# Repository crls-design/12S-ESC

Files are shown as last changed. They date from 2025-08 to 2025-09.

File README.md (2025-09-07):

# 12S ESC

This repository provides a low-cost, open-source design for a 12S Electronic Speed Controller (ESC) geared towards heavy-lift multirotor applications. It is designed to work with [ESCape32](https://github.com/neoxic/ESCape32), an open-source 32-bit ESC firmware.

## Design Philosophy

The goal of this ESC design is to maximize the performance-to-cost ratio by utilizing readily available components and open-source firmware while maintaining electrical and thermal characteristics that meet or exceed those of commercial ESCs in the same class.

This project aims to offer a competitive alternative to proprietary ESCs used in drones, robotics, and other high-power applications.

## Specifications

- STM32G431 processor
- 24MHz HSE crystal resonator
- 12S input (up to 50.4V)
- Full support for [ESCape32](https://github.com/neoxic/ESCape32)

> [!NOTE]  
> Although these are designed for 12S, the actual hardware is rated for 100V which is nearly double.

## Gallery

<p align="center">
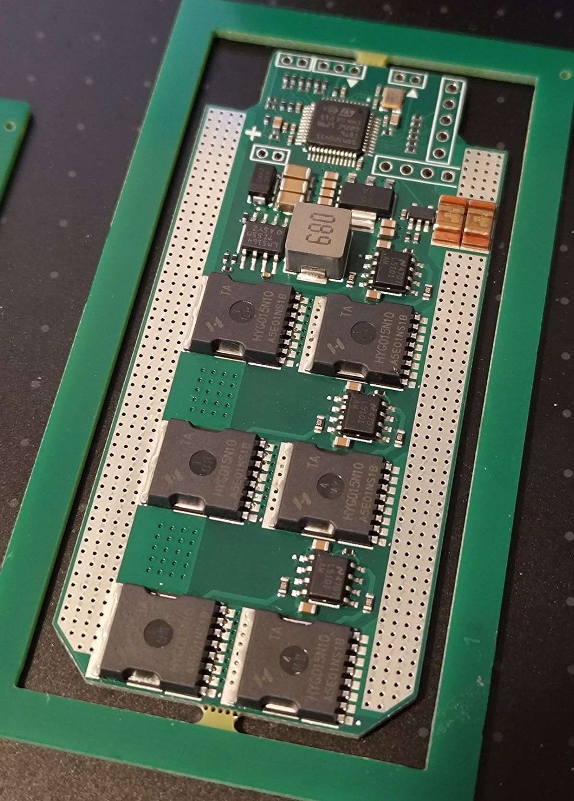
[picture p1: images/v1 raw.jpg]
    
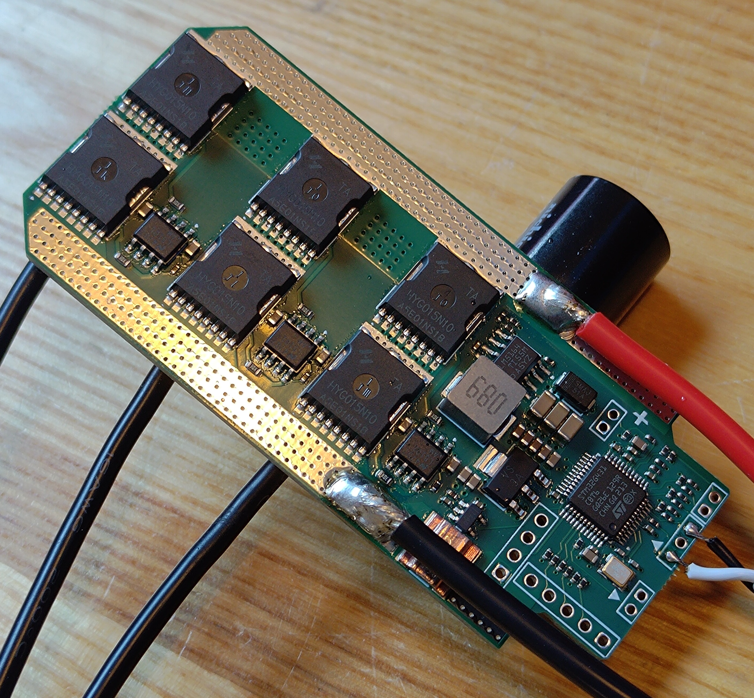
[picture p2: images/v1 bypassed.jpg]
    
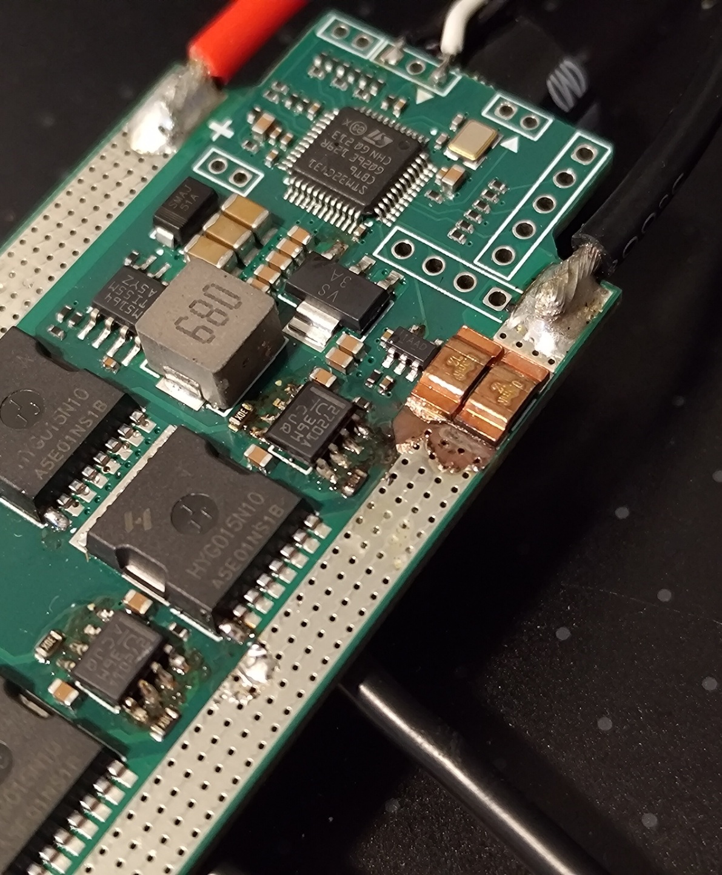
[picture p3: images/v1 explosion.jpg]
    
    </br>
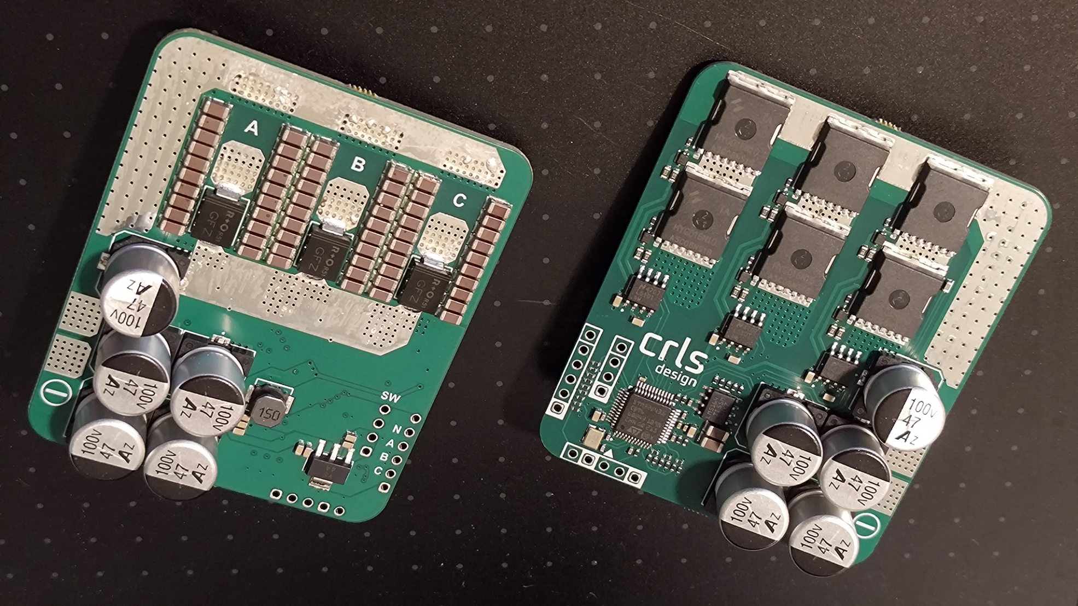
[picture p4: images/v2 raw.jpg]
    
</p>

## Getting Started

See [Getting Started](./docs/getting-started.md) for instructions on flashing and setup.

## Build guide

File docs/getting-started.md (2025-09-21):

# Getting Started

## Flashing and Setup

For blank STM32s, these are the general steps to get the board up and running:

1. Configuring the option bytes.
2. Flashing the appropriate bootloader.
3. Flashing the firmware.

> [!WARNING]  
> Do **not** power the board with a battery before completing these steps. The gate drivers do not have shoot-through protection, and powering prematurely will damage the MOSFETs.

### Prerequisites

- ST-LINK
- [STM32CubeProgrammer](https://www.st.com/en/development-tools/stm32cubeprog.html)

### Option Bytes

1. Always run from flash.

    - BOOT_LOCK = 1

2. Disable read/write protection (if not set by default).

    - RDP = AA (Level 0)
    - Flash protection = disabled

### Bootloader

 Get the latest `BOOT4_PA2` bootloader binary from [https://github.com/neoxic/ESCape32/releases](https://github.com/neoxic/ESCape32/releases) and flash at address `0x08000000`.

### Firmware

Build the following baseline target(s) and flash at address `0x08001000`.

**v1:**

```
add_target(CRLS1 STM32G431 DEAD_TIME=240 COMP_MAP=123 HALL_MAP=0xB450 SENS_MAP=0xB2A6A7 VOLT_MUL=3130 CURR_MUL=20 TEMP_ADC2 TEMP_CHAN=12 TEMP_FUNC=NTC10K3455UP2K USE_XOR USE_HSE=24 DUTY_SPUP=10 DUTY_RATE=5 FREQ_MIN=24 FREQ_MAX=24 TELEM_MODE=1 TELEM_POLES=2)
```

**v2:**

```
add_target(CRLS2 STM32G431 DEAD_TIME=160 COMP_MAP=231 HALL_MAP=0xB450 SENS_MAP=0xB2A6A7 VOLT_MUL=3130 TEMP_ADC2 TEMP_CHAN=12 TEMP_FUNC=NTC10K3455UP2K USE_XOR USE_HSE=24 DUTY_SPUP=10 DUTY_RATE=10 PROT_TEMP=90 FREQ_MIN=24 FREQ_MAX=24 TELEM_MODE=1 TELEM_POLES=2)
```

### Resources on Installation

[ESCape32's Installation Wiki Page](https://github.com/neoxic/ESCape32/wiki/Installation)

[Building ESCape32 on Windows](https://github.com/adrianblakey/slot-car-ecom/wiki/Building-ESCape32-on-Windows)

## Settings and Configuration

Under rapid deceleration on 50V input, the back electromotive force (BEMF) may exceed hardware voltage ratings. This was observed during no-load testing with a bench power supply. To mitigate this, limiting `duty_rate` to `0.5%/ms` is recommended.

> [!TIP]
> In real-world scenarios with a battery under load, this condition is less likely due to voltage sag and the battery acting as a load.

### Resources on Settings and Configuration

[ESCape32's Configuration Wiki Page](https://github.com/neoxic/ESCape32/wiki/Configuration)

[ESCape32's Settings Wiki Page](https://github.com/neoxic/ESCape32/wiki/Settings)

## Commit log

2025-08-07 add design files
    [1 top.SchDoc, 12S ESC.PrjPcb, 2 power supply.SchDoc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]
2025-08-08 update target string
    [3 mcu.SchDoc]
2025-08-31 remove target string from schematic
    [12S ESC.PrjPcb, 3 mcu.SchDoc]
2025-08-31 add v2 design files
    [1 top.SchDoc, 12S ESC.PrjPcb, 2 power supply.SchDoc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]
